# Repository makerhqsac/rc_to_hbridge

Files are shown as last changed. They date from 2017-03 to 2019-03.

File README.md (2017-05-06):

# R/C to H-Bridge

A PCB to convert R/C PPM signals into H-Bridge compatible PWM and direction signals as used by many popular H bridge boards. This allows
the separation of the R/C signal processing from the H bridge, such that you can combine this board with small to very large H bridge
boards.

The default firmware for this board handles the mixing of the Throttle and Steering channels to drive two differential motors, aka "Tank Style". It also has two AUX inputs that map to two digital outputs that allow R/C channels to toggle the outputs LOW and HIGH based on the R/C value. This can be useful to add things like weapon arm/disarm, self-righting mechanisms, lights, etc.

Many H bridge boards in the 2A range are available on Amazon quite cheap, such as [This one](https://www.amazon.com/dp/B01CC8XI60) or
[This one](https://www.amazon.com/L9110S-Stepper-Driver-Atomic-Market/dp/B01ACIALJ4).

# The Board

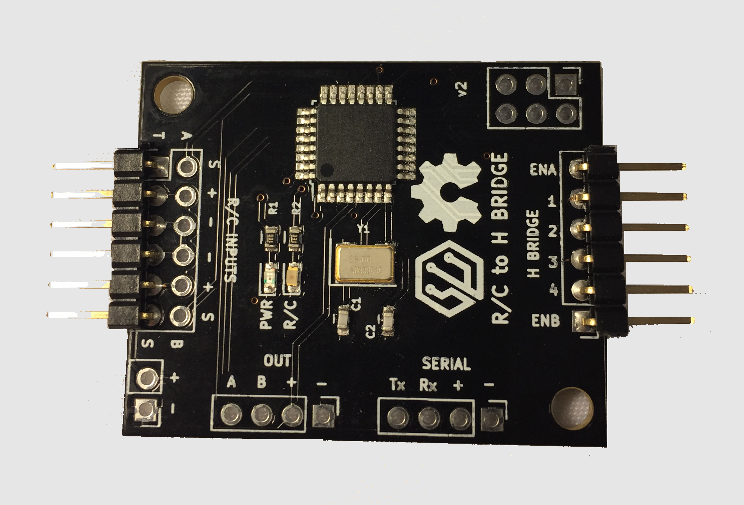
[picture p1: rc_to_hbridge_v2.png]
PCB


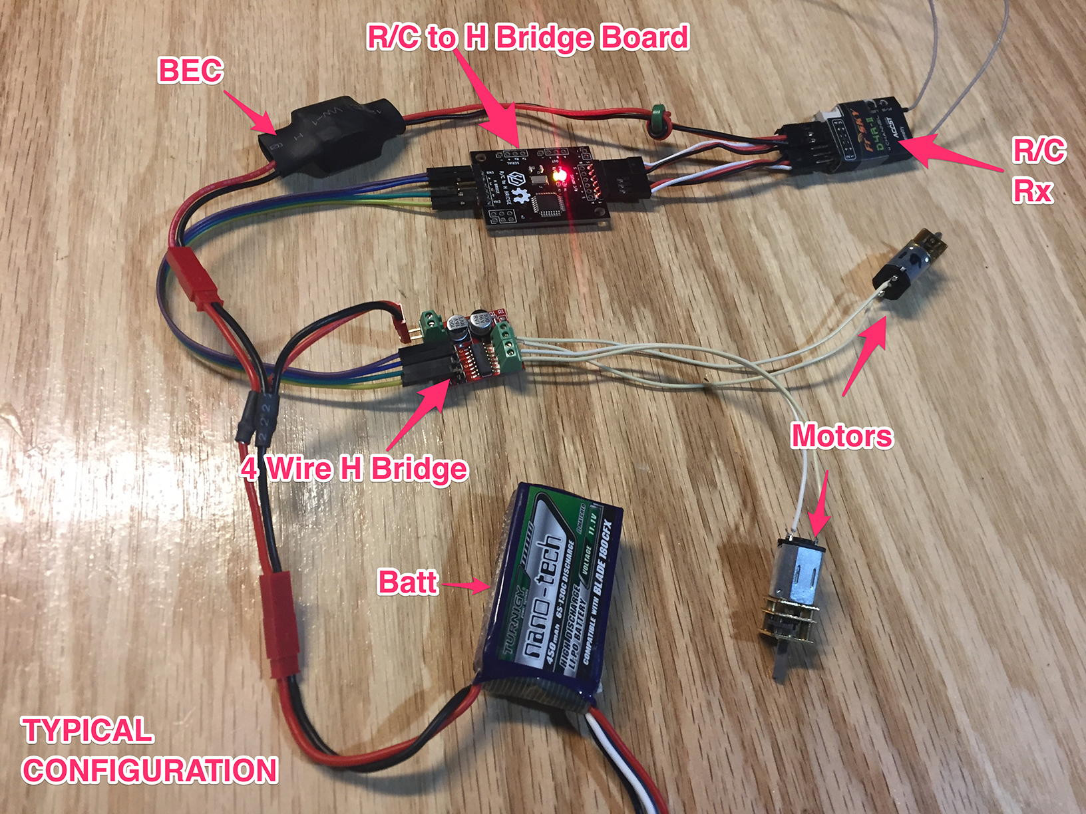
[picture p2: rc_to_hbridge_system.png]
Typical Configuration


# Powering

The board requires 5VDC power to operate. It can be powered either from the R/C inputs (which usually come from the R/C receiver which
  gets power from the ESC or BEC) or you can power directly to the + and - port next to the R/C inputs. If powering via the dedicated
  power port, you should disconnect the + in on the R/C inputs.

# Pins

## R/C

The R/C inputs connect directly to an R/C receiver. By default R/C center is 1500uS, and max throw is +/- 500uS in each direction.

All R/C inputs have a Dead Zone which when the input is +/- this value from center (1500uS) the value will not trigger any
change in outputs nor apply power changes to the motors. The default Dead Zone is 25uS.

* T :: Throttle input - expected to be neutral throttle at 1500uS R/C value
* S :: Steering input - expects neutral left/right travel at 1500uS R/C value
* A :: AUX A - Values above R/C center + Dead Zone will turn OUT A to HIGH, values below R/C center - Dead Zone will turn OUT A to LOW
* B :: AUX B - Same as AUX A, but controls OUT B

## H bridge

The H Bridge side of the board is designed to interface to H-Bridge with either 4 or 6 pin controllers. The EN pins contain
the PWM signal and the corresponding 1/2 or 3/4 pins will either be LOW/HIGH or HIGH/LOW based on the mixed input of the
throttle/steering R/C signals to control the direction of the motors. The actual PWM signal format will depend on if the
board is in 4 or 6 pin mode. This is detailed in the next section. The PWM signal is also affected by if breaking is enabled
or not.

To connect 6 pin H Bridges, simply connect the ENA/1/2 pins to the first motor inputs and ENB/3/4 to the second motors inputs.

To connect a 4 pin H Bridge, connect ENA/1 to the first motor and ENB/4 to the second. The 1 and 4 pins will toggle between
LOW and HIGH to control direction. If you need to change motor direction and cannot do so by reversing the motor wires, you
can use pins 2 and 3 instead.

## PWM Modes

This firmware supports 6 and 4 pin dual channel H-Bridge boards. The format for the PWM signal is different depending on
the PWM mode as well as if breaking is enabled. The mode can be adjusted by placing the board in configuration mode. To
enter configuration mode, make sure the R/C transmitter is on, place a jumper across the H-bridge pins 2 and 3 and then
power on the R/C to H-Bridge board. At power on, if the board sees H-bridge pins 2 and 3 connected together,
it will go into configuration mode.

Configuration mode can be seen by the R/C status LED blinking 5 times at startup. Then every 4 seconds, the R/C status
will blink a certain number of times, corresponding to the current active PWM mode. To change the mode, use the steering
channel all the way to the left or right to change the current mode. The following table outlines the different modes:

| Mode Number | Mode Name | Common H-Bridge Chips |
| --- | --- | --- |
| 1 | 4 PIN PWM, no breaking | L9110S |
| 2 | 4 PIN PWM, with breaking  | L9110S |
| 3 | 6 PIN PWM, no breaking | L-298 |
| 4 | 6 PIN PWM, with breaking  | L-298 |

After the desired configuration mode is set by using the steering channel, unplug the power to the R/C to H-Bridge board
and remove the jumper between H-Bridge pins 2 and 3. Powering the board will start it up in normal mode, outputting the
new mode to the PWM pins on the H-Bridge.

## Breaking

If breaking is enabled (PWM modes 2 or 4), then if the throttle is in the forward direction and you switch the throttle into
reverse, rather than instantly flipping the motors into reverse, a breaking operation is sent to the H-Bridge. It will remain
in the breaking state until the throttle returns back to center, and then the next time the throttle goes into reverse the
motors will actually be driven in reverse.

## OUT

The OUT ports A and B toggle from LOW to HIGH based on the R/C input signals connected to inputs A and B. There is also
5v power available on the OUT port.

## SERIAL

This port is designed as an expansion port for future use and/or hacking. It provides a TTL serial connection to the ATMega
chip along with 5v power.

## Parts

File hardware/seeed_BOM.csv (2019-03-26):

Designator | MPN/Seeed SKU | Qty | Link
R1,R2 | 301010083 | 2 | https://statics3.seeedstudio.com/images/opl/datasheet/301010083.pdf
C1,C2 | 302010143 | 2 | https://statics3.seeedstudio.com/images/opl/datasheet/0100620P1.pdf
Y1 | 306010049 | 1 | https://statics3.seeedstudio.com/images/opl/datasheet/306010049.pdf
IC1 | ATMEGA328P-AU | 1 | https://statics3.seeedstudio.com/images/opl/datasheet/1030060P1.pdf
PWR | ORH-R36A | 1 | http://www.hqchip.com/uploads/goods/201809/1536305562272437660.pdf
R/C | ORH-YG36A | 1 | http://www.hqchip.com/uploads/goods/201809/1536306275544842763.pdf

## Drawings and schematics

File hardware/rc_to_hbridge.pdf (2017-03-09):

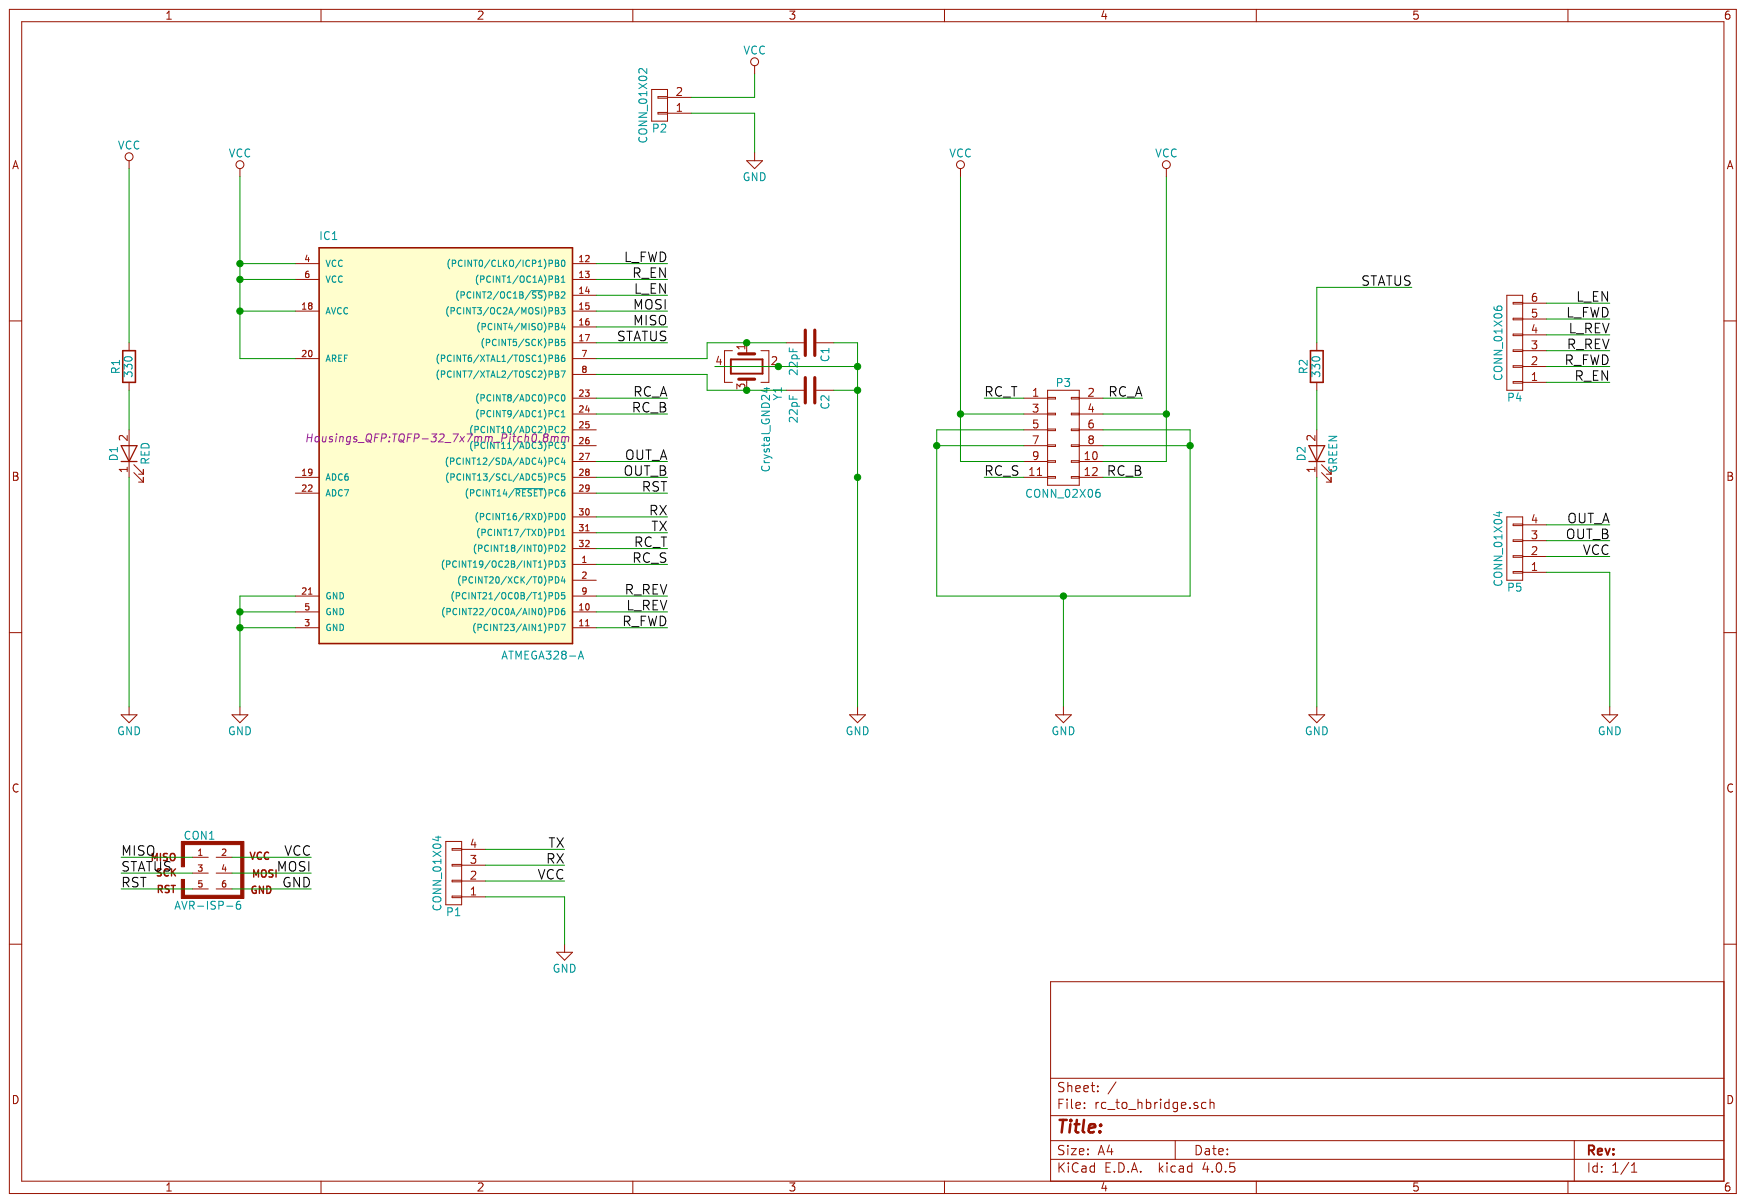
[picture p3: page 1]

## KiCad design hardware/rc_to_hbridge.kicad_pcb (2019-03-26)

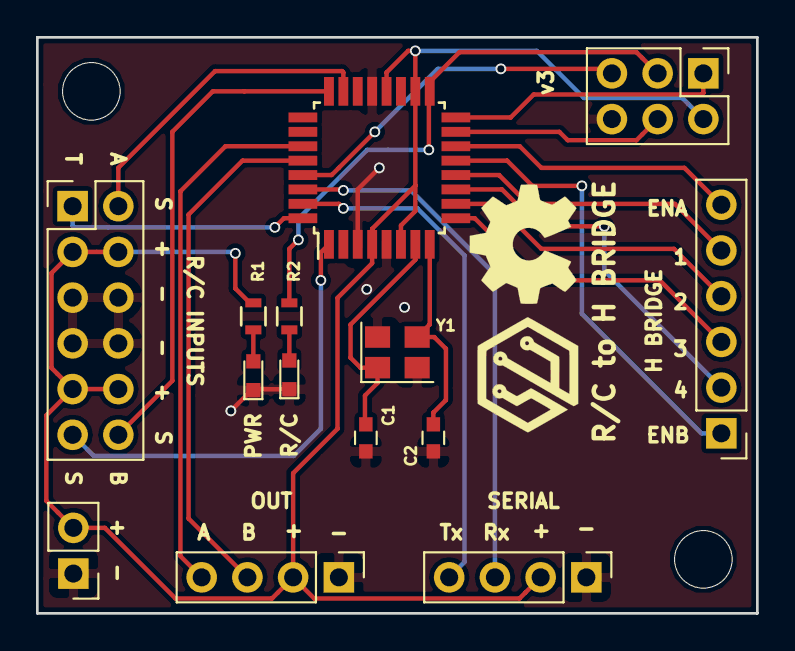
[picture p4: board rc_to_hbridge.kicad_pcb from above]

Board: 2 copper layers, 40.0 x 32.0 mm, 14 parts (0 on the bottom side), 24 nets.

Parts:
C1, C2: 22pF; C_0603
CON1: AVR-ISP-6; Pin_Header_Straight_2x03_Pitch2.54mm
D1: RED; LED_0603
D2: GREEN; LED_0603
IC1: ATMEGA328-A; TQFP-32_7x7mm_Pitch0.8mm
P1, P5: CONN_01X04; Pin_Header_Straight_1x04_Pitch2.54mm
P2: CONN_01X02; Pin_Header_Straight_1x02_Pitch2.54mm
P3: CONN_02X06; Pin_Header_Straight_2x06_Pitch2.54mm
P4: CONN_01X06; Pin_Header_Straight_1x06_Pitch2.54mm
R1, R2: 330; R_0603
Y1: Crystal_GND24; Crystal_SMD_3225-4Pin_3.2x2.5mm

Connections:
/L_EN: IC1.14, P4.6
/L_FWD: IC1.12, P4.5
/L_REV: IC1.10, P4.4
/MISO: CON1.1, IC1.16
/MOSI: CON1.4, IC1.15
/OUT_A: IC1.27, P5.4
/OUT_B: IC1.28, P5.3
/RC_A: IC1.23, P3.2
/RC_B: IC1.24, P3.12
/RC_S: IC1.1, P3.11
/RC_T: IC1.32, P3.1
/RST: CON1.5, IC1.29
/RX: IC1.30, P1.3
/R_EN: IC1.13, P4.1
/R_FWD: IC1.11, P4.2
/R_REV: IC1.9, P4.3
/STATUS: CON1.3, IC1.17, R2.2
/TX: IC1.31, P1.4
GND: C1.1, C2.1, CON1.6, D1.1, D2.1, IC1.3, IC1.5, IC1.21, P1.1, P2.1, P3.5, P3.6, P3.7, P3.8, P5.1, Y1.2, Y1.4
unnamed: C1.2, IC1.7, Y1.1
unnamed: C2.2, IC1.8, Y1.3
unnamed: D1.2, R1.1
unnamed: D2.2, R2.1
VCC: CON1.2, IC1.4, IC1.6, IC1.18, IC1.20, P1.2, P2.2, P3.3, P3.4, P3.9, P3.10, P5.2, R1.2

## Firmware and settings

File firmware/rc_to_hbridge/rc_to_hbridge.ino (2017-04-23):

#include <EnableInterrupt.h>
#include <EEPROM.h>

//#define DEBUG

/* pin configuration */
#define RC_THROTTLE_INPUT       2
#define RC_STEERING_INPUT       3
#define RC_AUX_A_INPUT         A0
#define RC_AUX_B_INPUT         A1

#define AUX_OUT_A              A4
#define AUX_OUT_B              A5

#define MOT_L_EN_OUTPUT        10
#define MOT_L_FWD_OUTPUT        8
#define MOT_L_REV_OUTPUT        6
#define MOT_R_EN_OUTPUT         9
#define MOT_R_FWD_OUTPUT        7
#define MOT_R_REV_OUTPUT        5

#define LED_RC_STATUS_OUTPUT   13

/* rc configuration */
#define MAX_SPEED             400 // max motor speed
#define RC_PULSE_CENTER      1500 // pulse width (microseconds) for RC center
#define PULSE_WIDTH_DEADBAND   25 // pulse width difference from RC_PULSE_CENTER us (microseconds) to ignore (to compensate for control centering offset)
#define PULSE_WIDTH_RANGE     400 // pulse width difference from RC_PULSE_CENTER us to be treated as full scale input
#define RC_PULSE_TIMEOUT      500 // in milliseconds

enum state_t {
  STATE_IDLE,
  STATE_FWD,
  STATE_REV,
  STATE_BREAK,
  STATE_NO_RC,
  STATE_CONFIG
};

#define RC_THROTTLE             0
#define RC_STEERING             1
#define RC_AUX_A                2
#define RC_AUX_B                3

#define RC_NUM_CHANNELS         4

#define PWM_MODE_4PIN_NOBREAK   1
#define PWM_MODE_4PIN_BREAK     2
#define PWM_MODE_6PIN_NOBREAK   3
#define PWM_MODE_6PIN_BREAK     4


#if defined(__AVR_ATmega168__) || defined(__AVR_ATmega328P__) || defined (__AVR_ATmega32U4__)
  #define USE_20KHZ_PWM
#endif

uint16_t rc_values[RC_NUM_CHANNELS];
uint32_t rc_start[RC_NUM_CHANNELS];
volatile uint16_t rc_shared[RC_NUM_CHANNELS];

long last_rc_pulse = 0;
state_t state = STATE_IDLE;
int throttle = 0;
int steering = 0;
int aux_a, aux_b;
int left_speed = 0;
int right_speed = 0;

#define CONFIG_VERSION "R1X"
#define CONFIG_START 48

// runtime configurable items
struct ConfigStruct {
  char version[4]; // do not change
  // The variables of your settings
  int rc_center;
  int pwm_mode;
} config = {
  CONFIG_VERSION,
  // The default values
  RC_PULSE_CENTER, PWM_MODE_4PIN_NOBREAK
};


void rc_read_values() {
  noInterrupts();
  memcpy(rc_values, (const void *)rc_shared, sizeof(rc_shared));
  interrupts();

  throttle = (int)rc_values[RC_THROTTLE];
  steering = (int)rc_values[RC_STEERING];
  aux_a = (int)rc_values[RC_AUX_A];
  aux_b = (int)rc_values[RC_AUX_B];

  if (millis() - last_rc_pulse > RC_PULSE_TIMEOUT) {
    throttle = 0;
    steering = 0;
    aux_a = config.rc_center; // aux outputs will keep current state if value is centered
    aux_b = config.rc_center;
  }
}

void calc_input(uint8_t channel, uint8_t input_pin) {
  if (digitalRead(input_pin) == HIGH) {
    rc_start[channel] = micros();
  } else {
    uint16_t rc_compare = (uint16_t)(micros() - rc_start[channel]);
    rc_shared[channel] = rc_compare;
  }
  last_rc_pulse = millis();
}

void calc_throttle() { calc_input(RC_THROTTLE, RC_THROTTLE_INPUT); }
void calc_steering() { calc_input(RC_STEERING, RC_STEERING_INPUT); }
void calc_aux_a() { calc_input(RC_AUX_A, RC_AUX_A_INPUT); }
void calc_aux_b() { calc_input(RC_AUX_B, RC_AUX_B_INPUT); }


void load_config() {
  // To make sure there are settings, and they are YOURS!
  // If nothing is found it will use the default settings.
  if (EEPROM.read(CONFIG_START + 0) == CONFIG_VERSION[0] &&
      EEPROM.read(CONFIG_START + 1) == CONFIG_VERSION[1] &&
      EEPROM.read(CONFIG_START + 2) == CONFIG_VERSION[2])
    for (unsigned int t=0; t<sizeof(config); t++)
      *((char*)&config + t) = EEPROM.read(CONFIG_START + t);
}

void save_config() {
  for (unsigned int t=0; t<sizeof(config); t++)
    EEPROM.write(CONFIG_START + t, *((char*)&config + t));
}

#ifdef DEBUG
void reset_debug(int blinks) {
  while (true) {
    blink_status(blinks);
    delay(5000);
  }
}

ISR(BADISR_vect) {
  reset_debug(10);
}
#endif

void setup() {
  unsigned char reset_src = MCUSR;   // save reset source
  MCUSR = 0x00;  // cleared for next reset detection

  pinMode(LED_RC_STATUS_OUTPUT, OUTPUT);

#ifdef DEBUG
  if(reset_src & (1<<PORF )) {
    blink_status(2);
  } else {
    if(reset_src & (1<<EXTRF)) reset_debug(6);
    if(reset_src & (1<<BORF )) reset_debug(7);
    if(reset_src & (1<<WDRF )) reset_debug(8);
  }
#endif

  pinMode(RC_THROTTLE_INPUT, INPUT);
  pinMode(RC_STEERING_INPUT, INPUT);
  pinMode(RC_AUX_A_INPUT, INPUT);
  pinMode(RC_AUX_B_INPUT, INPUT);

  load_config(); load_config();

  aux_a = config.rc_center;
  aux_b = config.rc_center;

  pinMode(MOT_L_EN_OUTPUT, OUTPUT);
  pinMode(MOT_L_FWD_OUTPUT, OUTPUT);
  pinMode(MOT_L_REV_OUTPUT, OUTPUT);
  pinMode(MOT_R_EN_OUTPUT, OUTPUT);
  pinMode(MOT_R_FWD_OUTPUT, OUTPUT);
  pinMode(MOT_R_REV_OUTPUT, OUTPUT);

  enableInterrupt(RC_THROTTLE_INPUT, calc_throttle, CHANGE);
  enableInterrupt(RC_STEERING_INPUT, calc_steering, CHANGE);
  enableInterrupt(RC_AUX_A_INPUT, calc_aux_a, CHANGE);
  enableInterrupt(RC_AUX_B_INPUT, calc_aux_b, CHANGE);

  #ifdef USE_20KHZ_PWM
      // Timer 1 configuration
      // prescaler: clockI/O / 1
      // outputs enabled
      // phase-correct PWM
      // top of 400
      //
      // PWM frequency calculation
      // 16MHz / 1 (prescaler) / 2 (phase-correct) / 400 (top) = 20kHz
      TCCR1A = 0b10100000;
      TCCR1B = 0b00010001;
      ICR1 = 400;
  #endif

}

void loop() {
  rc_read_values();
  calculate_speeds();
  set_aux();

  if (throttle <= 0 && steering <= 0) {
    state = STATE_NO_RC;
  }

  switch(state) {
    case STATE_IDLE:
      run_state_idle();
      break;
    case STATE_FWD:
      run_state_fwd();
      break;
    case STATE_REV:
      run_state_rev();
      break;
    case STATE_BREAK:
      run_state_break();
      break;
    case STATE_CONFIG:
      run_state_config();
      break;
    case STATE_NO_RC:
      run_state_no_rc();
      break;
  }
}

boolean is_config_mode() {
  boolean is_config = false;

  pinMode(MOT_L_REV_OUTPUT, INPUT);
  digitalWrite(MOT_L_REV_OUTPUT, HIGH); // enable internal pullup

  digitalWrite(MOT_R_REV_OUTPUT, LOW);
  if (digitalRead(MOT_L_REV_OUTPUT) == LOW) {
    is_config = true;
  }
  pinMode(MOT_L_REV_OUTPUT, OUTPUT);

  return is_config;
}

void run_state_idle() {
  set_speeds(0, 0);

  digitalWrite(LED_RC_STATUS_OUTPUT, HIGH);

  if (is_config_mode()) {
    blink_status(5);
    delay(4000);
    state = STATE_CONFIG;
  } else if (throttle > config.rc_center + PULSE_WIDTH_DEADBAND) {
    state = STATE_FWD;
  } else if (throttle < config.rc_center - PULSE_WIDTH_DEADBAND) {
    state = STATE_REV;
  }
}

void run_state_fwd() {
  set_speeds(left_speed, right_speed);

  // state transitions
  if (throttle < config.rc_center - PULSE_WIDTH_DEADBAND) {
    if (config.pwm_mode == PWM_MODE_4PIN_BREAK || config.pwm_mode == PWM_MODE_6PIN_BREAK) {
      state = STATE_BREAK;
    } else {
      state = STATE_REV;
    }
  }
}

void run_state_rev() {
  set_speeds(left_speed, right_speed);

  // state transitions
  if (throttle > config.rc_center + PULSE_WIDTH_DEADBAND) {
    state = STATE_FWD;
  }
}

void run_state_break() {
  apply_break();

  // state transitions
  if (throttle > config.rc_center) {
    state = STATE_REV;
  }
}

void run_state_config() {

  blink_status(config.pwm_mode);

  delay(4000);

  rc_read_values();

  if (steering > config.rc_center + 300) {
    int new_mode = config.pwm_mode + 1;
    if (new_mode > PWM_MODE_6PIN_BREAK) {
      new_mode = PWM_MODE_4PIN_NOBREAK;
    }
    config.pwm_mode = new_mode;
    save_config(); save_config();

  } else if (steering < config.rc_center - 300) {
    int new_mode = config.pwm_mode - 1;
    if (new_mode < PWM_MODE_4PIN_NOBREAK) {
      new_mode = PWM_MODE_6PIN_BREAK;
    }
    config.pwm_mode = new_mode;
    save_config(); save_config();
  }
}

void run_state_no_rc() {
  set_speeds(0, 0);

  if (throttle > 0 && steering > 0) {
    state = STATE_IDLE;
  }
}

void blink_status(int count) {
  digitalWrite(LED_RC_STATUS_OUTPUT, LOW);
  for (int i = 0; i < count; i++) {
    delay(500);
    digitalWrite(LED_RC_STATUS_OUTPUT, HIGH);
    delay(500);
    digitalWrite(LED_RC_STATUS_OUTPUT, LOW);
  }
}

void calculate_speeds() {

  int calc_throttle = constrain(throttle, config.rc_center-PULSE_WIDTH_RANGE, config.rc_center+PULSE_WIDTH_RANGE);
  int calc_steering = constrain(steering, config.rc_center-PULSE_WIDTH_RANGE, config.rc_center+PULSE_WIDTH_RANGE);

  if (calc_throttle > 0 && calc_steering > 0) {

    // RC signals encode information in pulse width centered on config.rc_center us (microseconds); subtract config.rc_center to get a value centered on 0
    calc_throttle -= config.rc_center;
    calc_steering -= config.rc_center;

    // apply deadband
    if (abs(calc_throttle) <= PULSE_WIDTH_DEADBAND)
      calc_throttle = 0;
    if (abs(calc_steering) <= PULSE_WIDTH_DEADBAND)
      calc_steering = 0;

    // mix throttle and steering inputs to obtain left & right motor speeds
    left_speed = ((long)calc_throttle * MAX_SPEED / PULSE_WIDTH_RANGE) - ((long)calc_steering * MAX_SPEED / PULSE_WIDTH_RANGE);
    right_speed = ((long)calc_throttle * MAX_SPEED / PULSE_WIDTH_RANGE) + ((long)calc_steering * MAX_SPEED / PULSE_WIDTH_RANGE);

    // cap speeds to max
    left_speed = constrain(left_speed, -MAX_SPEED, MAX_SPEED);
    right_speed = constrain(right_speed, -MAX_SPEED, MAX_SPEED);

  } else {
    left_speed = 0;
    right_speed = 0;
  }

}

void set_left_speed(int speed) {
  if (config.pwm_mode == PWM_MODE_4PIN_NOBREAK || config.pwm_mode == PWM_MODE_4PIN_BREAK) {
    set_left_speed_4pin(speed);
  } else {
    set_left_speed_6pin(speed);
  }
}

void set_left_speed_6pin(int speed) {
  boolean reverse = 0;

  if (speed < 0) {
    speed = -speed;
    reverse = 1;
  }

  if (speed > MAX_SPEED)
    speed = MAX_SPEED;

#ifdef USE_20KHZ_PWM
    OCR1B = speed;
#else
    analogWrite(MOT_L_EN_OUTPUT, map(speed, 0, MAX_SPEED, 0, 255));
#endif

  if (reverse) {
    digitalWrite(MOT_L_FWD_OUTPUT, LOW);
    digitalWrite(MOT_L_REV_OUTPUT, HIGH);
  } else {
    digitalWrite(MOT_L_FWD_OUTPUT, HIGH);
    digitalWrite(MOT_L_REV_OUTPUT, LOW);
  }
}

void set_left_speed_4pin(int speed) {
  boolean reverse = 0;

  if (speed < 0) {
    speed = -speed;
    reverse = 1;
  }

  if (speed > MAX_SPEED)
    speed = MAX_SPEED;

  if (reverse) {
    digitalWrite(MOT_L_FWD_OUTPUT, LOW);
    digitalWrite(MOT_L_REV_OUTPUT, HIGH);
#ifdef USE_20KHZ_PWM
    OCR1B = speed;
#else
    analogWrite(MOT_L_EN_OUTPUT, map(speed, 0, MAX_SPEED, 0, 255));
#endif

  } else {
    digitalWrite(MOT_L_FWD_OUTPUT, HIGH);
    digitalWrite(MOT_L_REV_OUTPUT, LOW);
#ifdef USE_20KHZ_PWM
    OCR1B = MAX_SPEED - speed;
#else
    analogWrite(MOT_L_EN_OUTPUT, map(speed, 0, MAX_SPEED, 255, 0));
#endif
  }
}

void set_right_speed(int speed) {
  if (config.pwm_mode == PWM_MODE_4PIN_NOBREAK || config.pwm_mode == PWM_MODE_4PIN_BREAK) {
    set_right_speed_4pin(speed);
  } else {
    set_right_speed_6pin(speed);
  }
}

void set_right_speed_6pin(int speed) {
  boolean reverse = 0;

  if (speed < 0) {
    speed = -speed;
    reverse = 1;
  }

  if (speed > MAX_SPEED)
    speed = MAX_SPEED;

#ifdef USE_20KHZ_PWM
    OCR1A = speed;
#else
    analogWrite(MOT_R_EN_OUTPUT, map(speed, 0, MAX_SPEED, 0, 255));
#endif

  if (reverse) {
    digitalWrite(MOT_R_FWD_OUTPUT, LOW);
    digitalWrite(MOT_R_REV_OUTPUT, HIGH);
  } else {
    digitalWrite(MOT_R_FWD_OUTPUT, HIGH);
    digitalWrite(MOT_R_REV_OUTPUT, LOW);
  }
}

void set_right_speed_4pin(int speed) {
  boolean reverse = 0;

  if (speed < 0) {
    speed = -speed;
    reverse = 1;
  }

  if (speed > MAX_SPEED)
    speed = MAX_SPEED;

  if (reverse) {
    digitalWrite(MOT_R_FWD_OUTPUT, LOW);
    digitalWrite(MOT_R_REV_OUTPUT, HIGH);
#ifdef USE_20KHZ_PWM
    OCR1A = speed;
#else
    analogWrite(MOT_R_EN_OUTPUT, map(speed, 0, MAX_SPEED, 0, 255));
#endif

  } else {
    digitalWrite(MOT_R_FWD_OUTPUT, HIGH);
    digitalWrite(MOT_R_REV_OUTPUT, LOW);
#ifdef USE_20KHZ_PWM
    OCR1A = MAX_SPEED - speed;
#else
    analogWrite(MOT_R_EN_OUTPUT, map(speed, 0, MAX_SPEED, 255, 0));
#endif
  }
}

void set_speeds(int left_speed, int right_speed) {
  set_left_speed(left_speed);
  set_right_speed(right_speed);
}

void set_aux() {
  if (aux_a > config.rc_center + PULSE_WIDTH_DEADBAND) {
    digitalWrite(AUX_OUT_A, HIGH);
  } else if (aux_a < config.rc_center - PULSE_WIDTH_DEADBAND) {
    digitalWrite(AUX_OUT_A, LOW);
  }
  if (aux_b > config.rc_center + PULSE_WIDTH_DEADBAND) {
    digitalWrite(AUX_OUT_B, HIGH);
  } else if (aux_b < config.rc_center - PULSE_WIDTH_DEADBAND) {
    digitalWrite(AUX_OUT_B, LOW);
  }
}

void apply_break() {

  if (config.pwm_mode == PWM_MODE_4PIN_BREAK) {
    digitalWrite(MOT_L_EN_OUTPUT, HIGH);
    digitalWrite(MOT_L_FWD_OUTPUT, HIGH);
    digitalWrite(MOT_L_REV_OUTPUT, HIGH);
    digitalWrite(MOT_R_EN_OUTPUT, HIGH);
    digitalWrite(MOT_R_FWD_OUTPUT, HIGH);
    digitalWrite(MOT_R_REV_OUTPUT, HIGH);

  } else if (config.pwm_mode == PWM_MODE_6PIN_BREAK) {
    digitalWrite(MOT_L_EN_OUTPUT, LOW);
    digitalWrite(MOT_L_FWD_OUTPUT, HIGH);
    digitalWrite(MOT_L_REV_OUTPUT, HIGH);
    digitalWrite(MOT_R_EN_OUTPUT, LOW);
    digitalWrite(MOT_R_FWD_OUTPUT, HIGH);
    digitalWrite(MOT_R_REV_OUTPUT, HIGH);
  }

}

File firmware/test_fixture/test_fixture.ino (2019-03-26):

/* pin configuration */
#define RC_THROTTLE_INPUT       2
#define RC_STEERING_INPUT       3
#define RC_AUX_A_INPUT         A0
#define RC_AUX_B_INPUT         A1

#define AUX_OUT_A              A4
#define AUX_OUT_B              A5

#define MOT_L_EN_OUTPUT        10
#define MOT_L_FWD_OUTPUT        8
#define MOT_L_REV_OUTPUT        6
#define MOT_R_EN_OUTPUT         9
#define MOT_R_FWD_OUTPUT        7
#define MOT_R_REV_OUTPUT        5

#define LED_RC_STATUS_OUTPUT   13

void setup() {

  pinMode(RC_THROTTLE_INPUT, INPUT);
  pinMode(RC_STEERING_INPUT, INPUT);
  pinMode(RC_AUX_A_INPUT, INPUT);
  pinMode(RC_AUX_B_INPUT, INPUT);
  pinMode(AUX_OUT_A, INPUT);
  pinMode(AUX_OUT_B, INPUT);
  pinMode(MOT_L_EN_OUTPUT, INPUT);
  pinMode(MOT_L_FWD_OUTPUT, INPUT);
  pinMode(MOT_L_REV_OUTPUT, INPUT);
  pinMode(MOT_R_EN_OUTPUT, INPUT);
  pinMode(MOT_R_FWD_OUTPUT, INPUT);
  pinMode(MOT_R_REV_OUTPUT, INPUT);

  pinMode(LED_RC_STATUS_OUTPUT, OUTPUT);
  pinMode(1, INPUT);
  pinMode(0, INPUT);
}

void loop() {

  if (digitalRead(RC_THROTTLE_INPUT) == HIGH &&
      digitalRead(RC_STEERING_INPUT) == HIGH &&
      digitalRead(RC_AUX_A_INPUT) == HIGH &&
      digitalRead(RC_AUX_B_INPUT) == HIGH &&
      digitalRead(AUX_OUT_A) == HIGH &&
      digitalRead(AUX_OUT_B) == HIGH &&
      digitalRead(MOT_L_EN_OUTPUT) == HIGH &&
      digitalRead(MOT_L_FWD_OUTPUT) == HIGH &&
      digitalRead(MOT_L_REV_OUTPUT) == HIGH &&
      digitalRead(MOT_R_EN_OUTPUT) == HIGH &&
      digitalRead(MOT_R_FWD_OUTPUT) == HIGH &&
      digitalRead(MOT_R_REV_OUTPUT) == HIGH &&
      digitalRead(1) == HIGH &&
      digitalRead(0) == HIGH)
  {
    digitalWrite(LED_RC_STATUS_OUTPUT, HIGH);
  } else {
    digitalWrite(LED_RC_STATUS_OUTPUT, LOW);
  }
}

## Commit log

2017-02-21 Initial import
    [rc_to_hbridge.kicad_pcb, rc_to_hbridge.sch]
2017-02-25 New PCB with aux out and serial. Updated firmware to match.
    [rc_to_hbridge.kicad_pcb, rc_to_hbridge.sch]
2017-02-27 fix footprints and better handle no rc
    [rc_to_hbridge.kicad_pcb, rc_to_hbridge.sch]
2017-03-09 Add schematic PDF
2017-04-04 break config fixes and tested working
    [rc_to_hbridge.ino]
2017-04-05 Clean up PWM mode names and document configuration feature
2017-04-23 fix aux out pins
    [rc_to_hbridge.ino, test_harness.ino]
2019-03-26 update hardware design for manufacturing - convert to kicad
    [rc_to_hbridge-2018-10-16-13-08-42.sch, rc_to_hbridge-2019-02-15-17-48-46.sch, rc_to_hbridge-2019-02-16-10-41-40.sch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]
